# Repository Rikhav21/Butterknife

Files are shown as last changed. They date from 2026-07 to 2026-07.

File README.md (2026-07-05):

# Butterknife
**A custom coreXY diode laser**

## Pictures
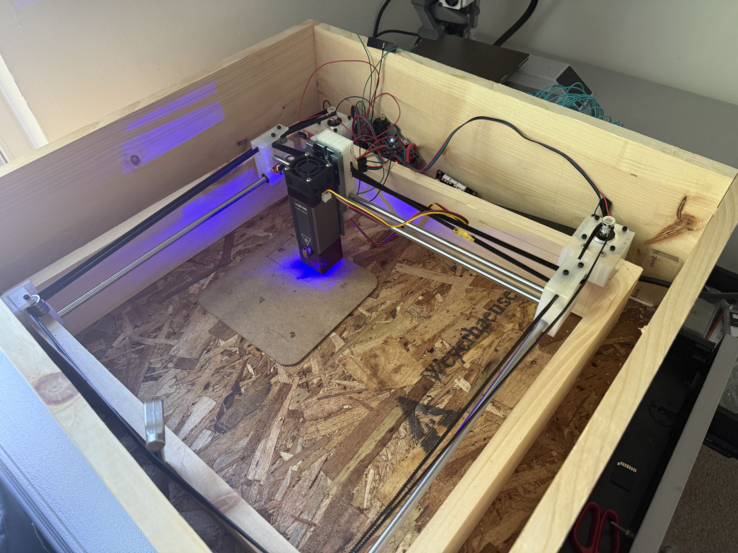
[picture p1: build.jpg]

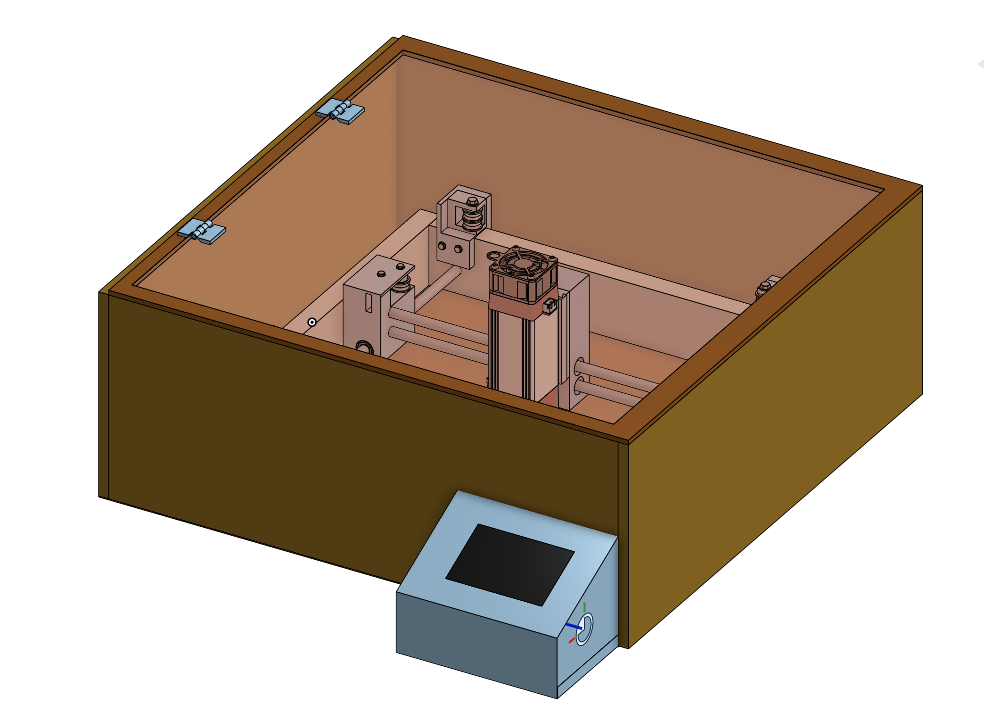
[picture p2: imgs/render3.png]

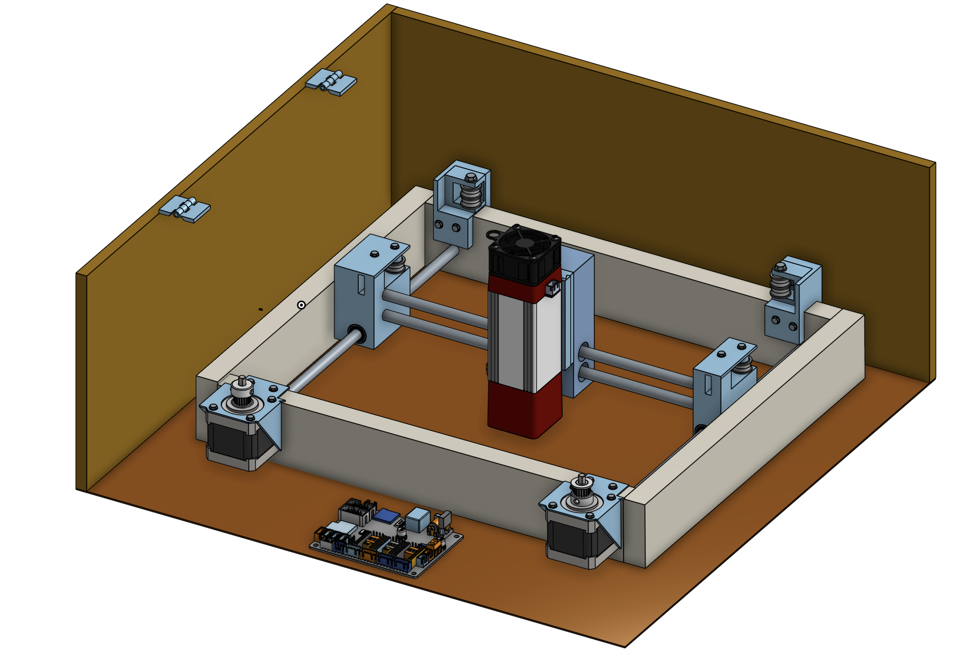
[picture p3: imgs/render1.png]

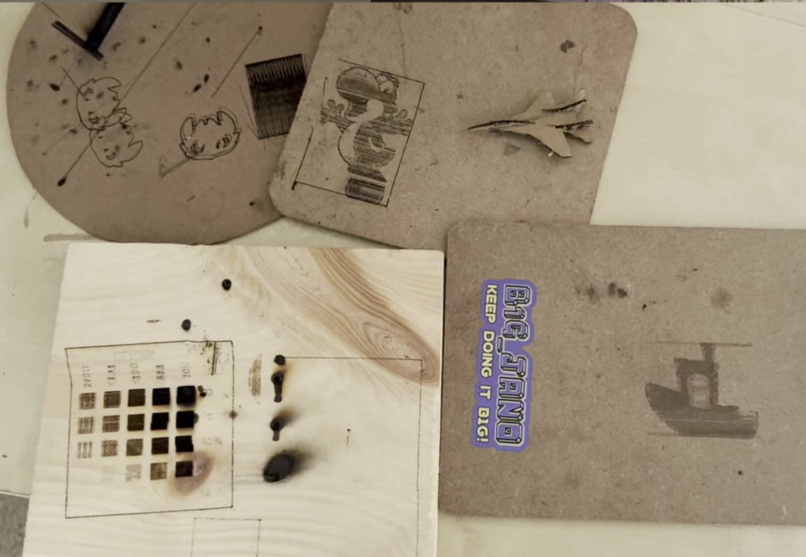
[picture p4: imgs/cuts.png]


## Hardware
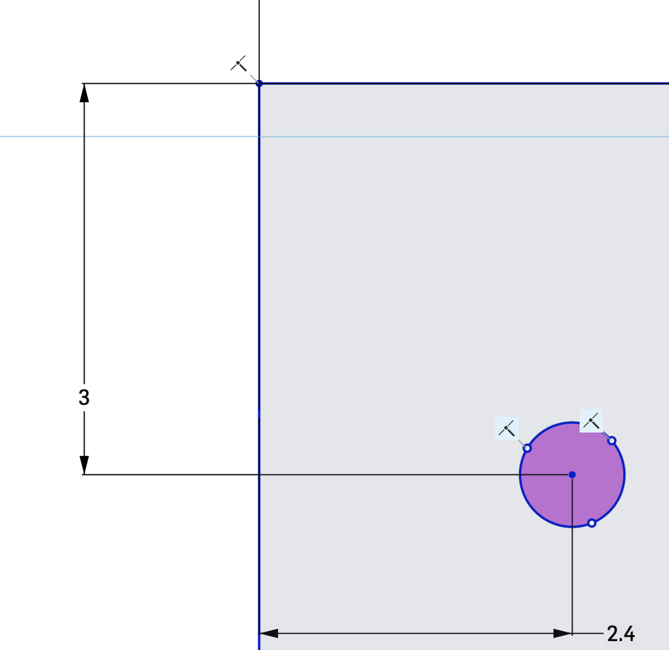
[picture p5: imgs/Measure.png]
You will need to cut the particle board into 2 pieces of 5.5x34 cm, and 2 pieces of 32x5.5 cm. Then use a drill to make 8mm holes according to the CAD, or this picture. 
Then assemble the CorreXY gantry according to the CAD. Afterwards, you can assemble the wood pieces into a square with the gantry inside. Then mount the motors and the belt tentioners. Lastly, route the belt and then you shuold be able to control it.

## Wiring
The wiring is extremely straightforward, Everything is connected to the DLC32 exactly as labeled, including the stepper mootors, endstops and the external power. The only thing is that oour llaesr is 10 W optical, so I used an external power wiring, where the laser driver is connected to teh PSU, and is connected to the laser pin and groound of the DLC32. Then the laser is connected directly to this driver. I just put the electronics in the outer box.

## Software
For the llaser cutter I am using a DLC32. Instead of using the stock firmware I use [FluidNC]([https://github.com/bdring/FluidNC](https://installer.fluidnc.com/fluidnc)) so that I can conotrol it over wifi. After installing flluidNC, you just need to update the config.yaml to the one in the firmware folder. Afterwards, you can access your laser at fluidnc.local, and control your laser from there. Afterwards, you can upload your gcoode. I personally used rayforge, but you can also use lightburn.  

[Here](https://cad.onshape.com/documents/d1304014e73009d6c11ef726/w/34172c7cf5d371a968e193e7/e/cf54ac2cfe94093a287dfb58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) is a link to my onshape CAD.
## BOM
| Part Name | Category | Price |
| :--- | :---| :---- |
| [Laser Motdule](https://www.ebay.com/itm/225549575372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) | 10 Watt | 149 |
| [Z axis](https://www.ebay.com/itm/225549575372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) | In the kit | 0 |
| [Stepper motors](https://www.aliexpress.us/item/3256808837281579.html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) | 3 pieces | 30 |
| [Inline fan](https://www.aliexpress.us/item/3256805856926717.html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) | 12 volt | 11 |
| [GT2 belt](https://www.aliexpress.us/item/3256807030412549.html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) | 5m | 6 |
| [Particle board](https://www.homedepot.com/p/Hardboard-Tempered-Panel-Common-1-8-in-4-ft-x-8-ft-Actual-0-115-in-x-47-7-in-x-95-7-in-832777/202189720) | 2x4 feet | 15 |
| [Idlers](https://www.aliexpress.us/item/3256803453717139.html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) | FR695 | 6 |
| [Pullies](https://www.aliexpress.us/item/2251832626304841.html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) | 16 teeth | 4 |
| [Laser controller](https://www.ebay.com/itm/225549575372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) | PWM | 0 |
| [Control board](https://www.aliexpress.us/item/3256804976730248.html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) | MKS DLC32 | 49 |
| [Motor drivers](https://www.aliexpress.us/item/3256804976730248.html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) | TMC2009 | 0 |
| [Laser sheild](https://www.aliexpress.us/item/3256807735248948.html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) | Actually welding| 20 |
| [Plug](https://www.aliexpress.us/item/3256806794776596.html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) | 3 wire | 13 |
| [Wire](https://www.aliexpress.us/item/3256808511247695.html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) | 12 gauge | 6 |
| [Wood screws](https://www.homedepot.com/p/Everbilt-6-x-1-1-2-in-Zinc-Plated-Phillips-Flat-Head-Wood-Screw-10-Pack-826871/317479436) | 20 pieces | 8 |
| [Control screen](https://www.aliexpress.us/item/3256804976730248.html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) | touchscreen | 7 |
Total cost 323

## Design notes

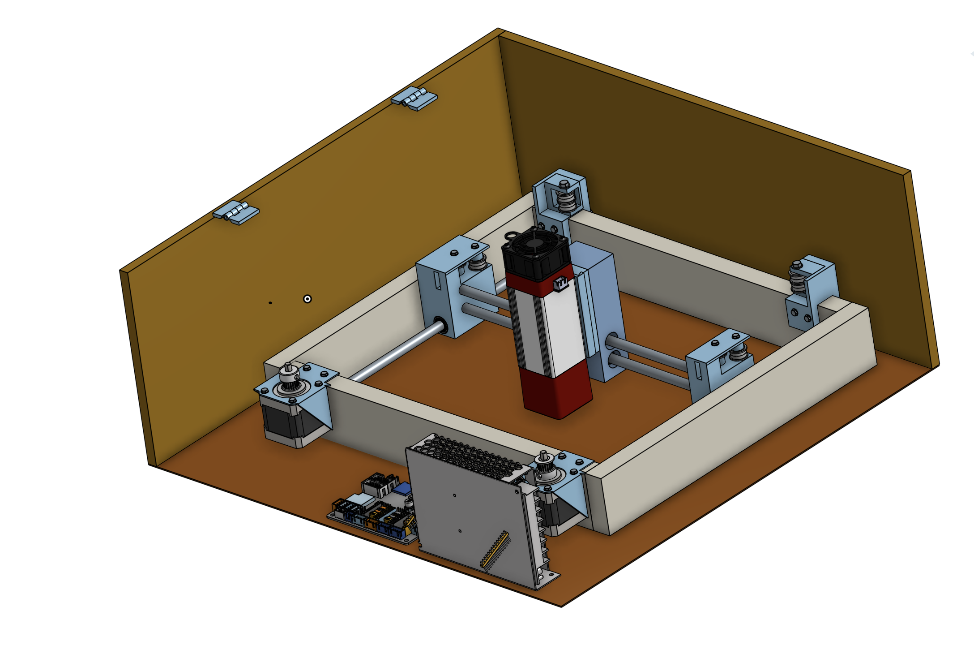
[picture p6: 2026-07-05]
imgs/render2.png

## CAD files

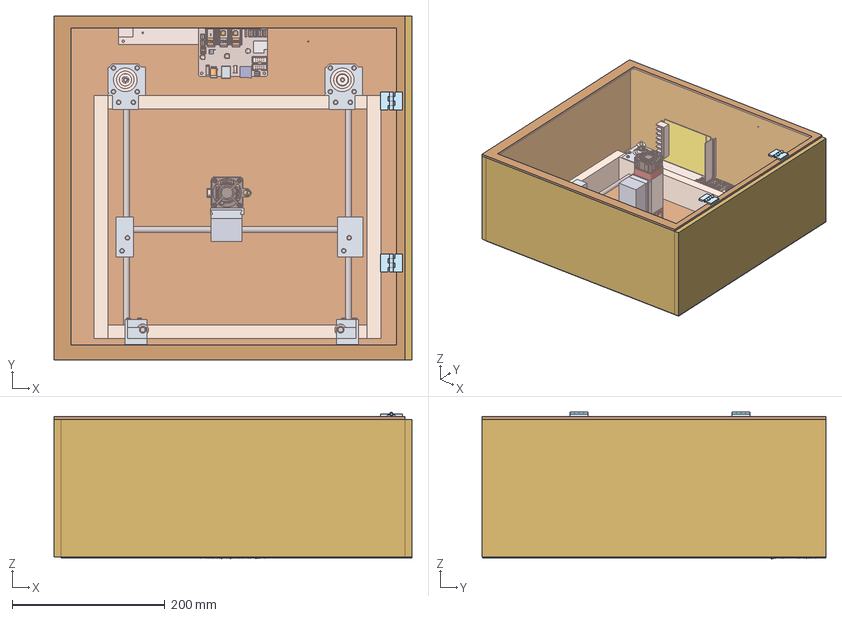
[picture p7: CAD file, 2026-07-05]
Full Assembly.step
468.0 x 450.0 x 191.7 mm
MKS DLC32 V2.1 x 170
Hex washer machine screw #4-40 x 0.5 x 15
F695 Bearing stack x 16
Hex washer machine screw #8-32 x 1 x 6
Hex washer machine screw #4-40 x 1 x 5
GT2_20T v1 (1) (1) x 2
Left XY x 2
LM8UU 8mm Linear Bearing_6 x 4
Linear Rod 300 x 4
lrs-100-5-body
lrs-100-5-board
Hex washer machine screw #6-40 x 0.125 x 2
Laser Tree - Modul - Diode
SUNON EB4020 x 3
M3x40 x 4
Laser Tree - Modul - SchutzgitterSLDPRT
Laser Tree - Modul - Luftd�se - Anschluss Typ A
Laser Tree - Modul - Extrusion
JST-Steckverbinder-3Pin
Laser Tree - Modul - PCB
JST-Steckverbinder-2Pin x 2
Laser Tree - Modul - K�hlk�rper
Laser Tree - Modul - Luftd�se
Laser Tree - Modul - Elektronikgeh�use
Laser Tree - Modul - Sichtschutz
Laser Tree - Modul - Diode - Schutzkappe
RES0805 x 4

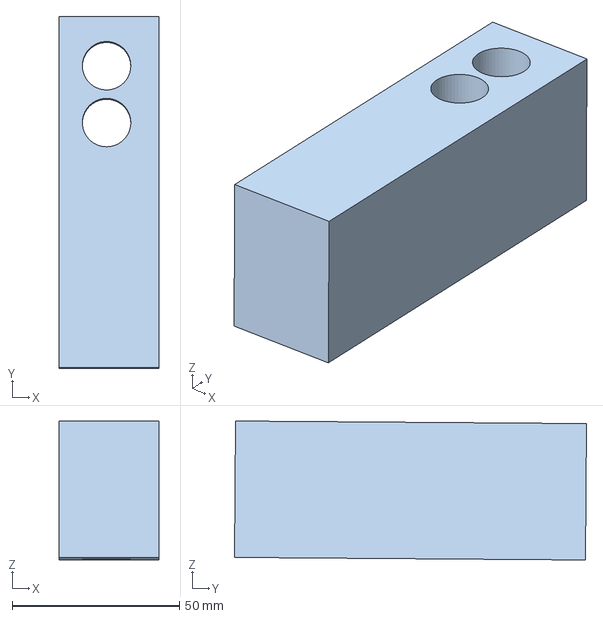
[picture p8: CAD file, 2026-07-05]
Parts to Print/Laser mount.step
30.0 x 105.3 x 41.6 mm

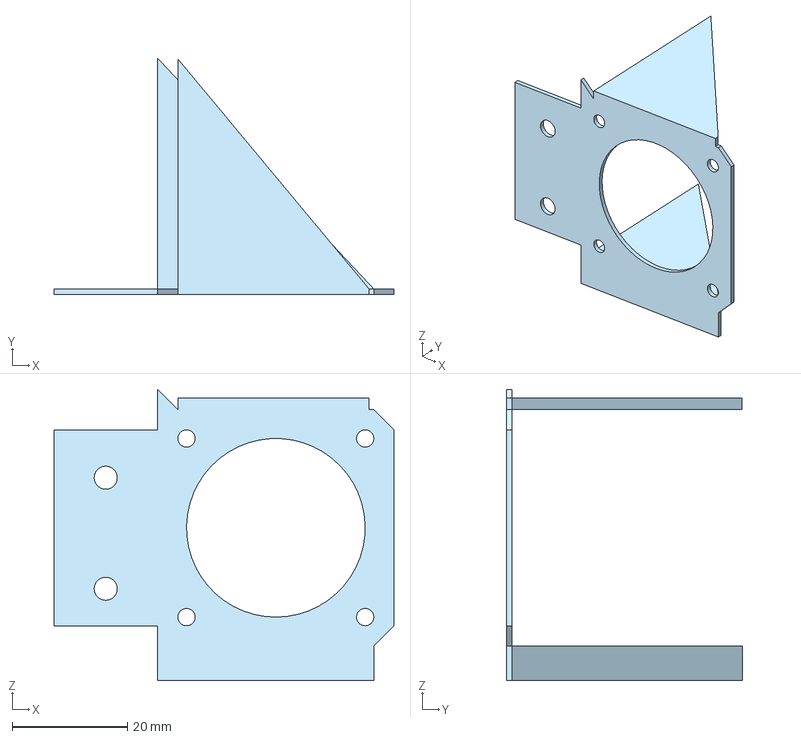
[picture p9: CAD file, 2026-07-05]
Parts to Print/Motor mount.step
59.0 x 41.0 x 50.5 mm

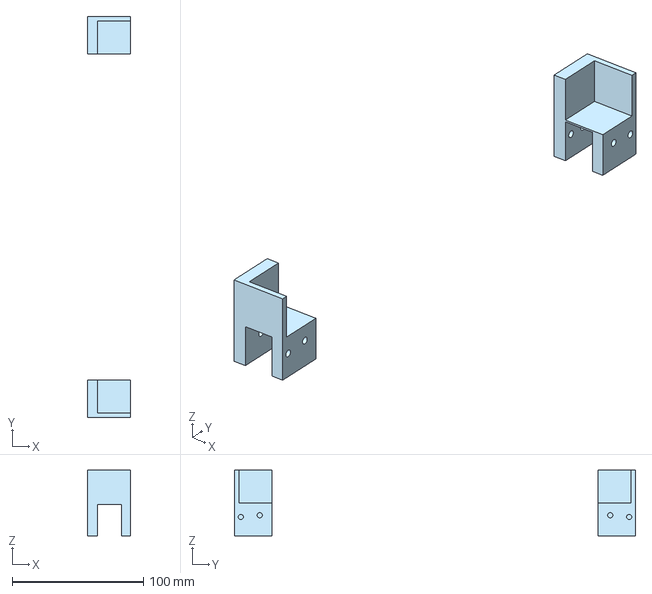
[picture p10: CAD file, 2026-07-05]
Parts to Print/Holders.step
32.9 x 305.7 x 50.0 mm

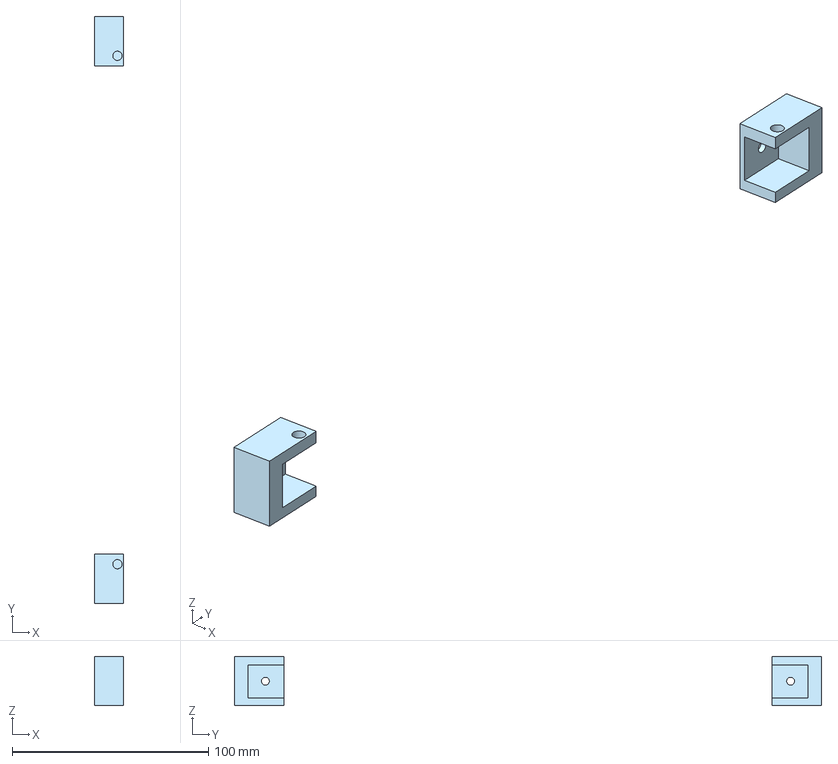
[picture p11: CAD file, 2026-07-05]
Parts to Print/Belt tensioner.step
15.0 x 298.8 x 25.0 mm

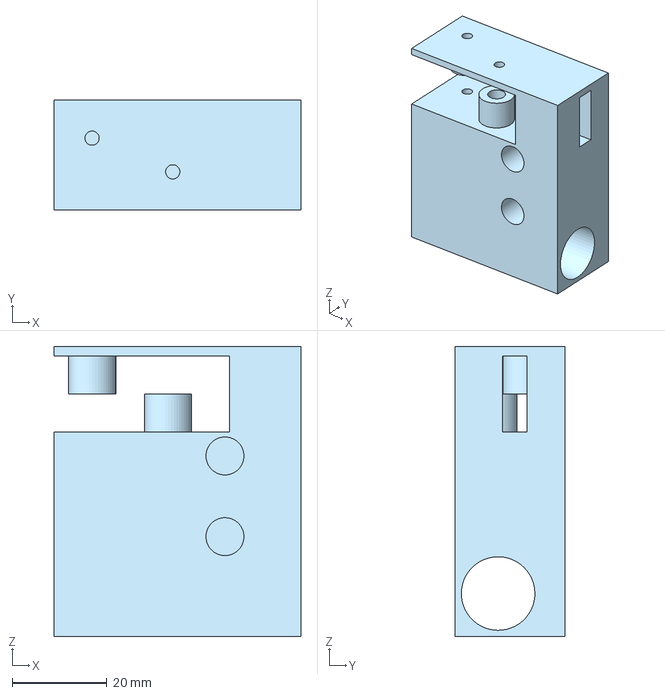
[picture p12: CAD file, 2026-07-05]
Parts to Print/Idlers Left.step
52.0 x 23.1 x 61.1 mm

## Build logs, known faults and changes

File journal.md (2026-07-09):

---
title: The butterknife
author: Rikhav
description: An actually safeish laser cutter
created_at: "2025-06-18"
---

# Butterknife
Total time spent: 56
## Day 1 (16/6/25 
Today I mainly just did research into how a laser cutter works, different mechanisms etc. Currently my idea is to just make a core XY, like the gantry of the printer that I designed a few months ago. I think tha tI will eaither go with 10 or 20 watts. And an enclosure is absolutely madatory. I got some plywood, and I am probably going to make the frame out of that.
""Total Time spent: 5 hours**

## Day 2 (17/6/25)
Today I started to work on the CAD of my laser cutter, did some research into potential parts, and desided that I am goign to use 20 Watts for my laser cutter. That takes up almost a forth of the budget, I think that I might be able to find a coupon or something. Also believe it or not I think that I will actually be done with the CAD tomorrow, so lets hope that I can get this approved relatively quick
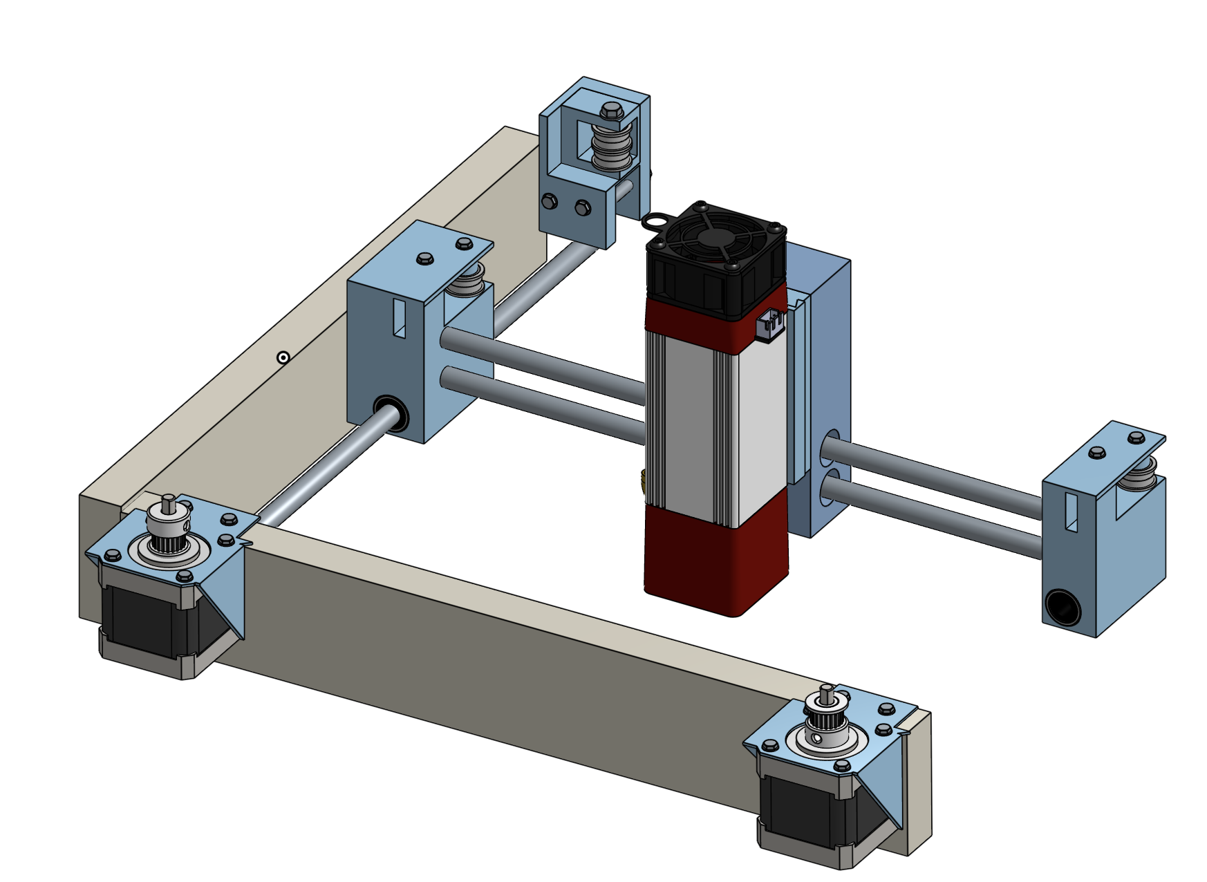
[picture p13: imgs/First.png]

""Total Time spent: 4 and a half hours**
## Day 3 (18/6/25)
Today I actually spent a lot of time recearching again, and I realized that lasers are actually a lot mor eexpensive than I thought. The "20" Watt laser that I was looking at actually only have 20 watts of input power, and the optical power was closer to 5 Watts. I am going to have to search more, because most of the cheaper lasers taht I was looking at do the same thing, so the laser might end up being one of the more expensive parts on this. On the other hand, I got some wood for the fram, and I finished up most of the CAD for the butterknife itself, but I still have the laser toolhead left, and outer encolosure. TOday it might not look like I did a lot, but a ton of research, parts finding, and just general replanning happened today.

""Total Time spent: 4 and a half hours**

## Day 4 (19/6/25)
Today I added my laser, the mount from the laser to the linear bearings, and I started making the enclosure. I completely overestimated how fast I could CAD, however I actually finished the entire curring setup, and now I just need to make the top of the laser case, and then I will be able to start with the PCB. I mounted both of the motors, and assembled pretty much everything. I want to make this a  reallly high quality project, so I will probably make the CAD as good as I can. I also want to make a PCB for a control screen, so that might also show effort.

""Total Time spent: 3 and a half hours**
## Day 5 (20/6/25)
Today I think that I finished the CAD of the laser cutter, and that I will be able to finish the COM tomorrow. I made the outer enclosure, and I might add a littl ebit more for airflow and other electronics like fans and a control board, however I think tha tI will be able to get this over with pretty soon, even though I am pretty sure that I said this in literally other journal entry. On the bright side most of the parts for my filament recyclen have already arrived so that I can submit this pretty soon. I also feel like the CAD could be a little bit more clean with tht ecoloring, however I want to ship this before THursday, so that I at least have a chance at those headphones.


**Total Time: 4 and a half hours**
## Day 6 (28/6/25)
Today was the first part of researnching and making the BOM. I got some of the parts that I need, but I mainly just spen my time searching for a laser. I decided on a 10 watt one, and I was able to get if for 140 dollars, with some other stuff that I will need along with the laser.
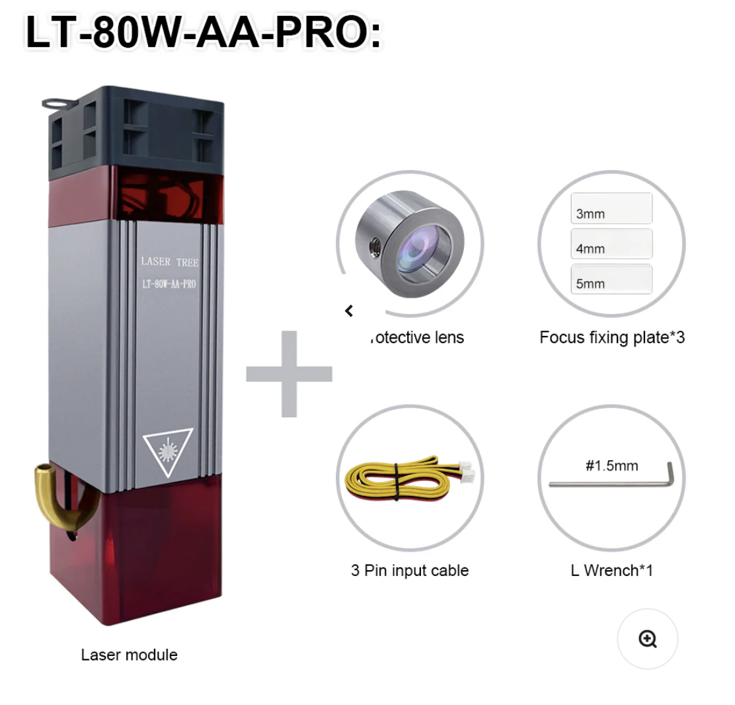
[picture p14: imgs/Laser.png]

**Total time spent: 3 and a half hours**

## Day 7 (29/6/25)
Today I am ready to submit my project, and finished my BOM. today I got everything done for the BOM, and i also finished the readME. I also postied everything in highway pitstop, and did more reasearch for my BOM. The total ended up costing 323 dollars which was more than I would have liked, but it still fits inside the budget.
** Total time spend: 5 and a hald hours**
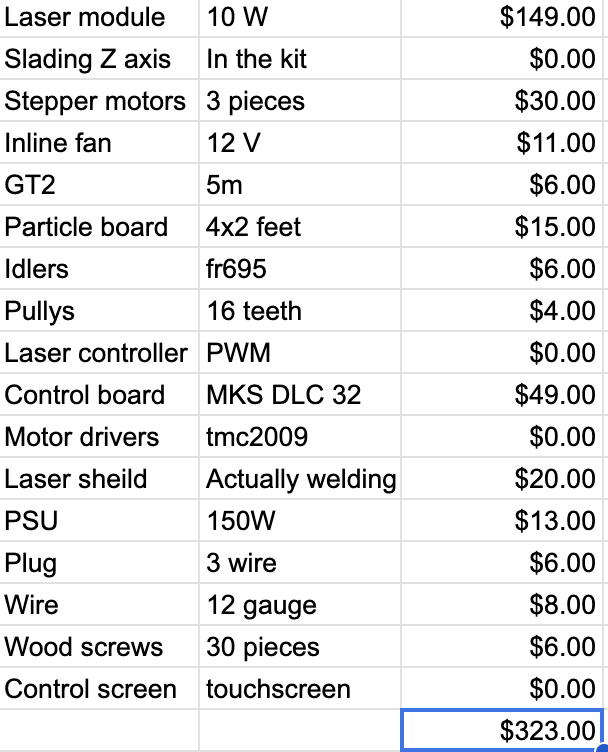
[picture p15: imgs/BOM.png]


## Day 8 (25/6/26)
After almost a year, I finally got around to building it. I had vacation from school today, so I dedicated the entire day to get this working. First, I worked on the electronic wiring while the printer was working on parts. I got the screen working and I was able to control the lasesrr over the web, on the default firmware. Afterwards, I assembled the gantry while other parts were printing. Although the X axis was a little rough, it lossened up a I secured it to the frame. I drilled out the mounts for the linear rods with a 8mm drill bit. After securing the gantry in the outer frame, I was able to move it pretty smoothlly, after adding on the belt, I realized that it wasn't llong enough as I was reusing from another projecct, so I psent a long time trying too extend it. I decided to try again tomorrow and actually get it done, because I literally spent the entire day on this.


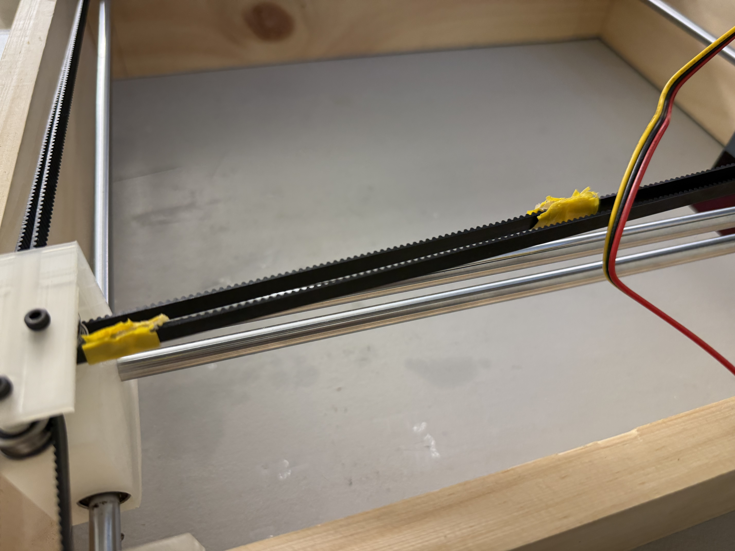
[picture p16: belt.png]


**Total time spent: 12 hours**

## Day 9 (26/6/26)
Today I was determined to finish the project, so I spent another day grinding. I added the limit switches and built the outer case. That was actually pretty fast. Then I worked on the firmware. I spent a long time trying to get fluidNC to work with the TFT that I got, but ultimately I was not able to, and actually installing fluidNC took a lot longer than I thought. However, I was able to get it on the wifi, and then I had to assign all of the pins and settings. After a bunch of troubleshooting, I finally got all of the controls to work. However, for some reason it wasn't working on chrome, so instead I had to access the port over safari or firefox. Afterwards, I also realized that I had to change the Gcode generator that I was using, as LaaerGRBL didn't work on Mac, so instead I had to use rayforge. For a while I was having a ton of softwarae and slicing issues. But when I finally got the got it moving, my bellt ssnapped, so I had to reattach and melt them together. I finally was able to try engraving, however it ended up pretty bandy, so that was something that I am going to fix to fix tomorrow, but for now I'm just happy it is recognizable.

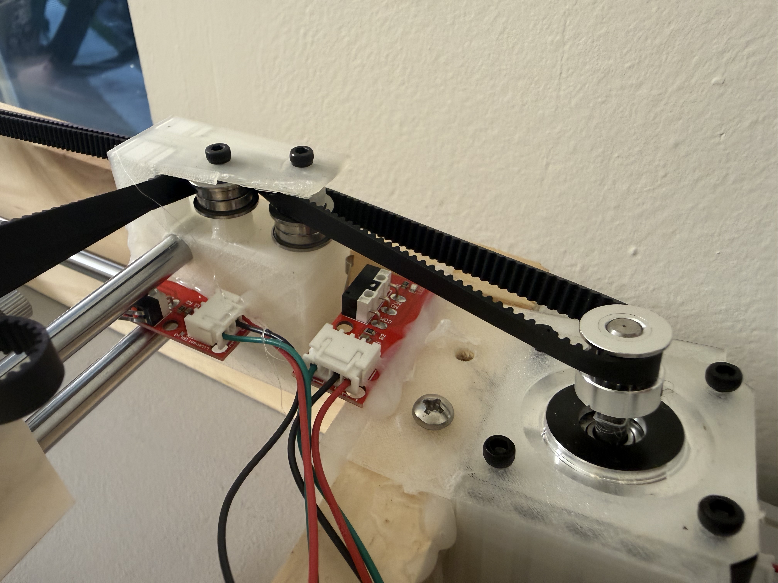
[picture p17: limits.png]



**Total Time spent 10 and a half hours**

## Day 10 (28/6/26)
After a break, I'm back on the frinid. I realiized that there wass a problen with the caridgess, and so I redesigned and reprinted them, and now it seems like they move smoother. i also changed the toolhend so that there isn't as much of a incline towards the toolhead. Other than that I only changed a few of the parts of firmware aboout speed and I did some calibrating for the speed and power on different aterials. I got a clean engraving, and even cut a kit card out of cardboard. Honestly, I felt like this was a success.
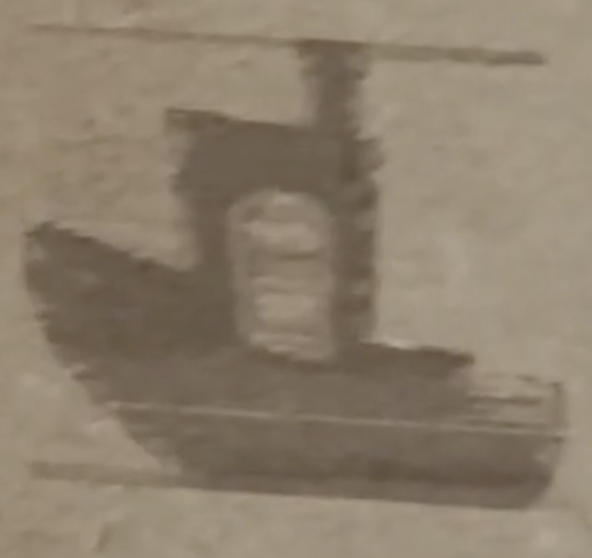
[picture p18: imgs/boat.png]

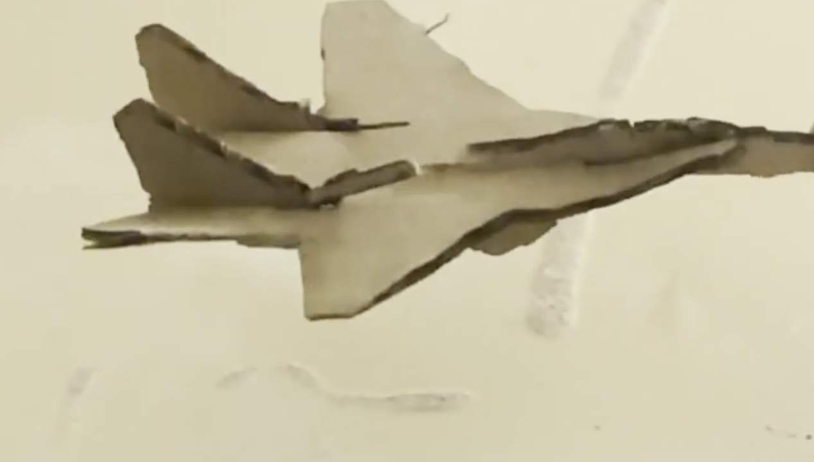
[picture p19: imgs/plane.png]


**Total time spent: 2 and a half hours.**

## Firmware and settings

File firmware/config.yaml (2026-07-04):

board: MKS-DLC32
name: ButterKnife
meta: Rikhav
kinematics:
  CoreXY: {}
stepping:
  engine: I2S_STATIC
  idle_ms: 254
  pulse_us: 6
  dir_delay_us: 10
  disable_delay_us: 0
axes:
  shared_stepper_disable_pin: i2so.0
  x:
    steps_per_mm: 80
    max_rate_mm_per_min: 5000
    acceleration_mm_per_sec2: 1000
    max_travel_mm: 313
    soft_limits: true
    homing:
      cycle: 1
      positive_direction: false
      mpos_mm: 0
      feed_mm_per_min: 300
      seek_mm_per_min: 600
      settle_ms: 500
      seek_scaler: 1.1
      feed_scaler: 1.1
    motor0:
      limit_neg_pin: gpio.36:low
      hard_limits: false
      pulloff_mm: 5
      stepstick:
        step_pin: i2so.1
        direction_pin: i2so.2:low
        disable_pin: NO_PIN
        ms1_pin: NO_PIN
        ms2_pin: NO_PIN
        ms3_pin: NO_PIN
      limit_pos_pin: NO_PIN
      limit_all_pin: NO_PIN
  y:
    steps_per_mm: 80
    max_rate_mm_per_min: 5000
    acceleration_mm_per_sec2: 1000
    max_travel_mm: 230
    soft_limits: true
    homing:
      cycle: 1
      positive_direction: false
      mpos_mm: 0
      feed_mm_per_min: 300
      seek_mm_per_min: 600
      settle_ms: 500
      seek_scaler: 1.1
      feed_scaler: 1.1
    motor0:
      limit_neg_pin: gpio.35:low
      hard_limits: false
      pulloff_mm: 5
      stepstick:
        step_pin: i2so.5
        direction_pin: i2so.6
        disable_pin: NO_PIN
        ms1_pin: NO_PIN
        ms2_pin: NO_PIN
        ms3_pin: NO_PIN
      limit_pos_pin: NO_PIN
      limit_all_pin: NO_PIN
i2so:
  bck_pin: gpio.16
  data_pin: gpio.21
  ws_pin: gpio.17
spi:
  miso_pin: gpio.12
  mosi_pin: gpio.13
  sck_pin: gpio.14
i2c0:
  sda_pin: gpio.00
  scl_pin: gpio.04
sdcard:
  cs_pin: gpio.15
  card_detect_pin: gpio.39
macros:
  macro0: $SD/Run=lasertest.gcode
  macro1: $SD/Run=home.gcode
coolant:
  flood_pin: NO_PIN
  mist_pin: NO_PIN
  delay_ms: 0
Laser:
  pwm_hz: 5000
  output_pin: gpio.32
  speed_map: 0=0.000% 2200=100.000%
user_outputs:
  analog0_pin: NO_PIN
  analog1_pin: NO_PIN
  analog2_pin: NO_PIN
  analog3_pin: NO_PIN
  analog0_hz: 5000
  analog1_hz: 5000
  analog2_hz: 5000
  analog3_hz: 5000
  digital0_pin: NO_PIN
  digital1_pin: NO_PIN
  digital2_pin: NO_PIN
  digital3_pin: NO_PIN
start:
  must_home: false
control: {}
